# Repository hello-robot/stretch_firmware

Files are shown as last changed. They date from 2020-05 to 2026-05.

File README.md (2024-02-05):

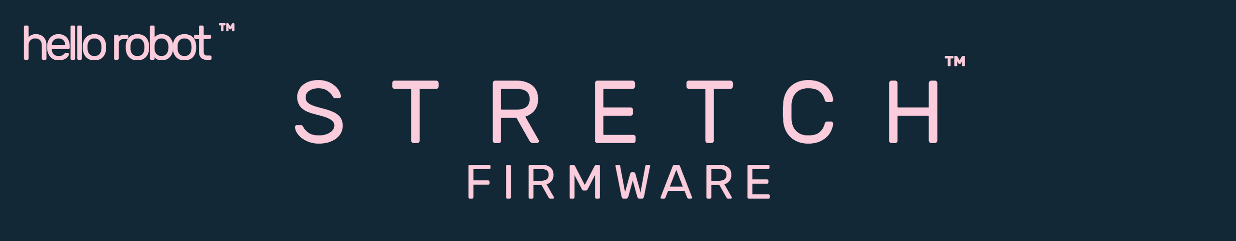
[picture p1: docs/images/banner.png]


# Overview
The [Stretch Firmware](https://github.com/hello-robot/stretch_firmware) repository provides the Arduino based firmware for the Stretch robot. 

Minor version updates to Stretch Body may occasionally require the robot's firmware to also be updated.

The repository includes the firmware for the three Stretch PCBA types: 

* hello_stepper: firmware for stepper motor controller based on the Mechaduino project
* hello_wacc: firmware for wrist accelerometer board (Wacc) in the wrist 
* hello_pimu:  firmware for power and imu board (Pimu) in the base

## License
For details, see the LICENSE.md file in the root directory. All materials within this repository are licensed with the [GNU General Public License v3.0 (GNU GPLv3)](https://www.gnu.org/licenses/gpl-3.0.html) except where other third-party licenses must apply.  

We thank people who have contributed to this work via open-source code and open hardware. We especially thank the [Mechaduino](https://tropical-labs.com/mechaduino/) project and [Tropical Labs](https://tropical-labs.com/). The motor controller firmware and hardware are derived from the excellent [firmware](https://github.com/jcchurch13/Mechaduino-Firmware) and [hardware](https://github.com/jcchurch13/Mechaduino-Hardware) created for the Mechaduino project by Tropical Labs.

------
<div align="center"> All materials are Copyright 2022-2024 by Hello Robot Inc. Hello Robot and Stretch are registered trademarks. The Stretch robots are covered by U.S. Patent 11,230,000 and other patents pending.</div>

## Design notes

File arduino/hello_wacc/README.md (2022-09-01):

# Stretch RE1/RE2 - Wacc Firmware

The Stretch Wacc Firmware runs on the Wacc PCBA found inside the robot arm. Wacc stands for the 'Wrist + Accelerometer' board. The Wacc firmware provides

* Monitoring of the wrist accelerometer
* Monitoring the Arduino expansion header in the wrist

The Wacc expansion header is electrically routed to potentially provide

* Analog in (x1)
* Digital in (x1)
* Digital out (x2)
* Serial SPI 
* Serial I2C 
* Serial UART

See the [Stretch RE1 Hardware User Guide](https://docs.hello-robot.com) for pin-out, electrical, and connector information.

## Using the Expansion DIO Header

### Factory Interface

By default the Expansion DIO header is configured in firmware to provide two digital inputs, two digital outputs, and an analog input. This can be seen in the [Wacc_status](https://github.com/hello-robot/stretch_firmware/blob/master/arduino/hello_wacc/Common.h) structure.

```c
struct __attribute__ ((packed)) Wacc_Status{
  float ax;	//Accelerometer AX
  float ay;	//Accelerometer AY
  float az;	//Accelerometer AZ
  int16_t a0; //expansion header analog in
  uint8_t d0; //expansion header digital in
  uint8_t d1; //expansion header digital in
  uint8_t d2; //expansion header digital out
  uint8_t d3; //expansion header digital out
  uint32_t single_tap_count; //Accelerometer tap count
  uint32_t state;
  uint32_t timestamp; //ms, overflows every 50 days
  uint32_t debug;
};
```

The user can interact with these pins through the [Stretch Body python interface](https://hello-robot.github.io/stretch_body_guide/). 

### Custom Interface

Advanced users may want to create a custom interface to the Expansion DIO header that utilizes SPI, I2C, or UART. For this, see the provided Stretch Firmware tutorials.

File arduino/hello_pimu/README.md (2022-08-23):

# Stretch RE1/RE2 - Pimu Firmware

The Stretch Pimu Firmware runs on the Pimu PCBA. Pimu stands for Power+IMU. The firmware is responsible for 

* Monitoring / filtering / calibration of 9DOF IMU 

* Battery voltage and current monitoring

* Buzzer

* Base case fan control

* Runstop monitoring

* Monitoring cliff sensors

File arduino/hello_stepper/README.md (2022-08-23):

# Stretch RE1/RE2 - Stepper Firmware

The Stretch Stepper Firmware runs on the Stepper PCBA found on the back of the Stretch stepper motors. It is a modified version of the open source [Mechaduino project](https://github.com/jcchurch13/Mechaduino-Firmware), which provides closed loop current control of a stepper motor.

The firmware is organized so as to allow switching, via serial command, between 'stock Mechaduino mode' with its menu interface and the Hello Robot firmware with its RPC interface.

The primary hardware modifications are:

* Higher current capacity by use of parallel motor drivers
* Locking JST connectors
* Addition of a 'sync' line for multi-dof synchronization

The primary software modifications are:

* RPC and serialization layer to manage controller parameters, controller commands, etc

* Trapezoidal trajectory generators based on the library [MotionGenerator](https://github.com/EmanuelFeru/MotionGenerator) 

* Handling of runstop and motor synchronization

* Implementation of a guarded move behavior

* Various controller variants, controller and parameter management functions

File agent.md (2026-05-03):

# Stretch Body AI Directives

You are currently operating inside the `stretch_firmware` repository (Core firmware for the Stretch RE1, Stretch 2, and Stretch 3 robot).

## Ecosystem Navigation
Do not guess hardware specifications or firmware behavior. If a user asks a question that requires knowledge outside of this  codebase, use your file system tools to navigate to the sibling repositories:
* **Master Knowledge Base (Datasheets/Tutorials):** `../stretch_knowledge_base`
* **Firmware Source Code:** `../stretch_body`

If these directories do not exist, politely inform the user that they can clone them from the Hello Robot GitHub into their `~/repos` folder for better assistance.

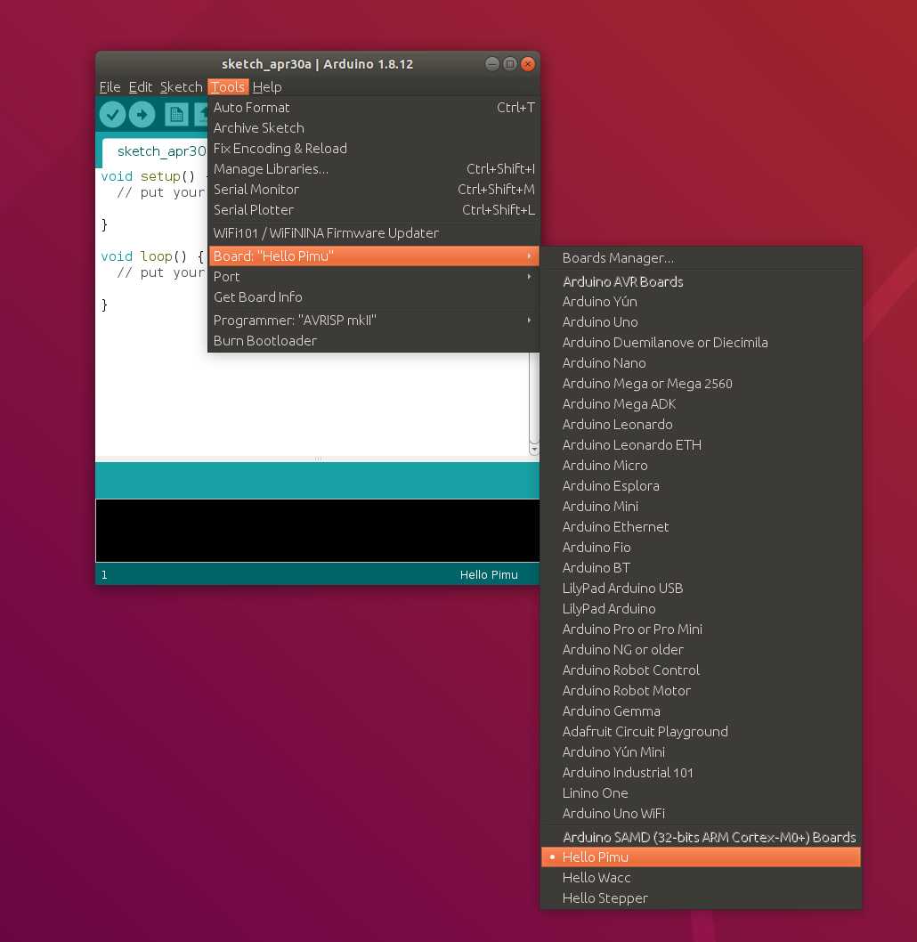
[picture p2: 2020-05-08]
docs/images/arduino-2.png

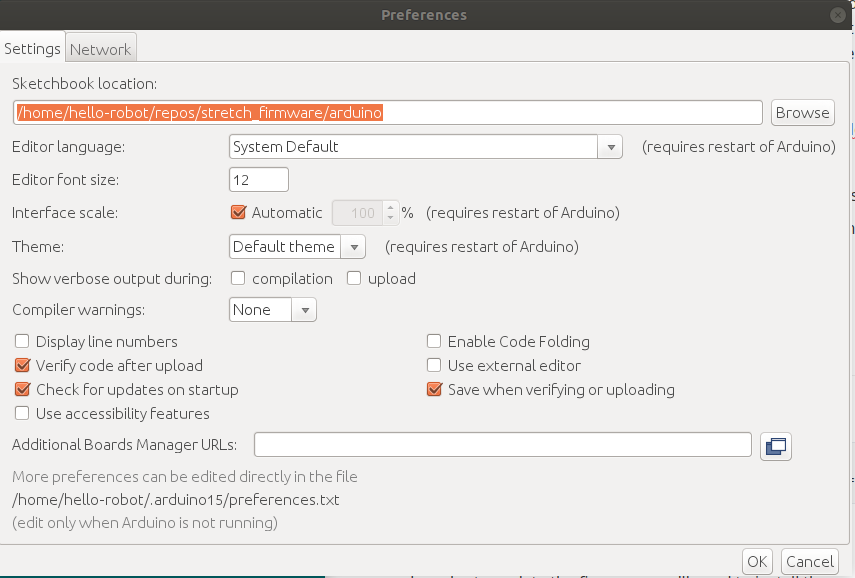
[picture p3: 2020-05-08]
docs/images/arduino-1.png

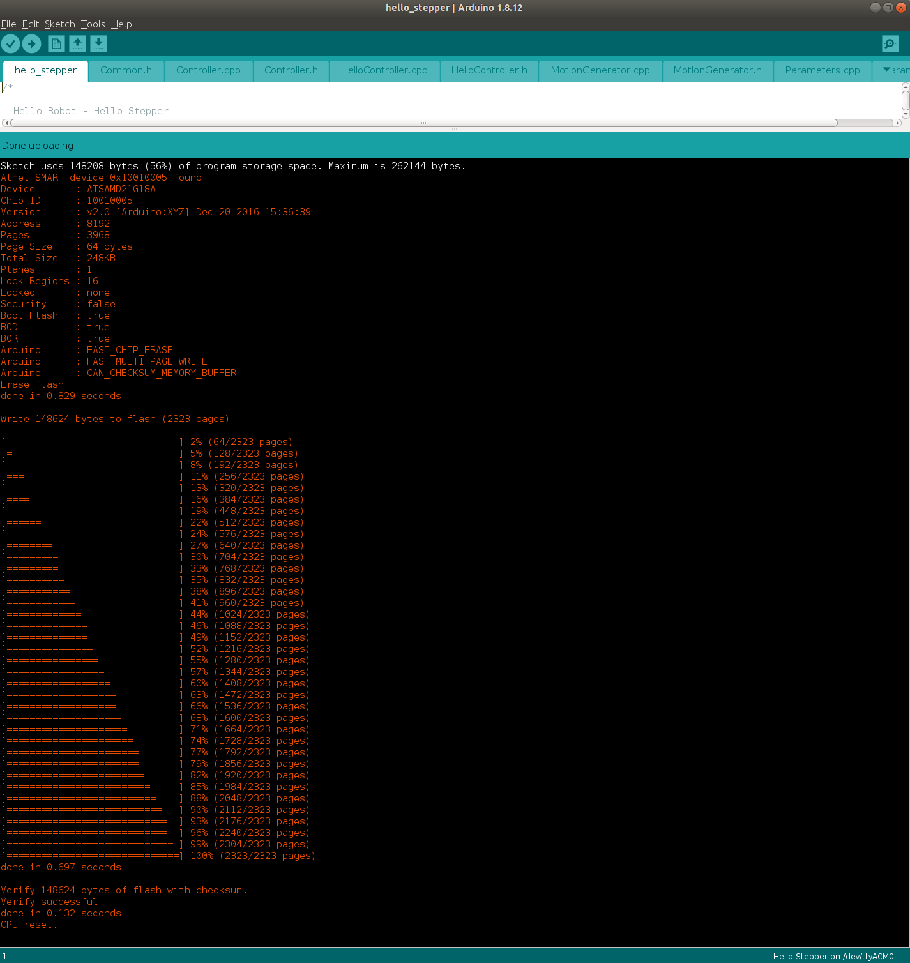
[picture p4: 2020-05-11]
docs/images/arduino-4.png

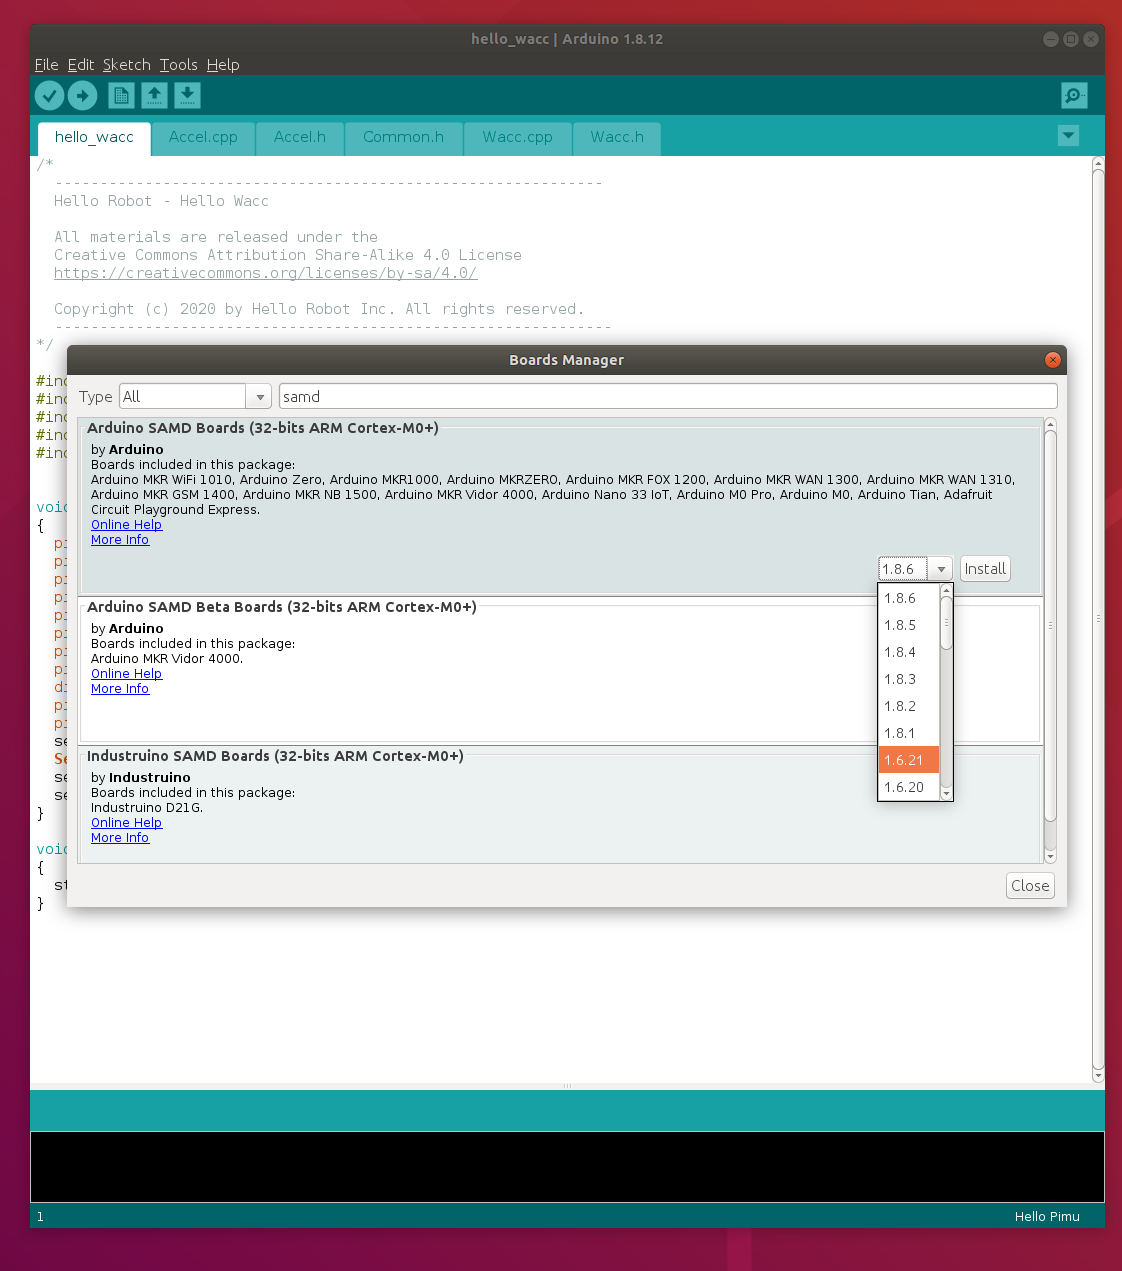
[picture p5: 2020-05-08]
docs/images/arduino-3.png

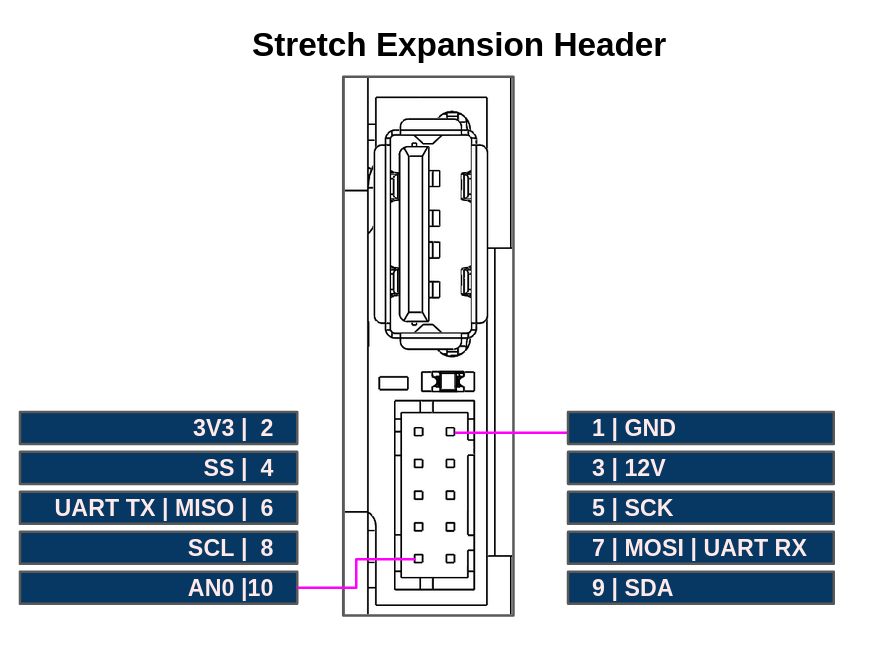
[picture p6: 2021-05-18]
docs/images/wrist_expansion_header.png

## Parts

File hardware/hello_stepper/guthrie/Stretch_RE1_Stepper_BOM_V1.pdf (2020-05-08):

Comment | Description | Designator
Hello_Robot_Logo
S2B-PH-SM4-TB(LF)(SN) | CONN HEADER SMD R/A 2POS 2MM | BRAKE
0.1UF 25V | CAP CER 0.1UF 25V Y5V 0603 | C1, C2, C3, C5, C10, C13, C18, C19
12PF 50V | CAP CER 12PF 50V C0G/NP0 0603 | C7, C8
1UF 25V | CAP CER 1UF 25V X5R 0603 | C9, C11, C12
0.22uF 50V | CAP CER 0.22UF 50V X5R 0603 | C16, C20
100uF 50V | CAP ALUM 100UF 20% 50V SMD | C17
Yellow | LED Yellow CLEAR SMD R/A | DBG
250mA | PTC RESET FUSE 16V 250MA 1206 | F1
0Ohm | JUMPER TIN SMD | GND
| M3 through hole | H1, H2, H3, H4
220 Ohm | FERRITE BEAD 220 OHM 0805 1LN | L1
470 OHM | FERRITE BEAD 470 OHM 0603 1LN | L2
S4B-XH-A(LF)(SN) | CONN HEADER R/A 4POS 2.5MM | MOTOR
HEADER-Shrouded-2X5-P127 | CONN HEADER SMD 10POS 1.27MM | PGM
S3B-XH-A(LF)(SN) | CONN HEADER R/A 3POS 2.5MM | POWER
BSS138 | MOSFET N-CH 60 V 320 mA | Q1
330 | RES SMD 330 OHM 5% 1/4W 0603 | R3
0.1Ohm | RES 0.1 OHM 1% 1/3W 1206 | R5, R6
1K | RES SMD 1K OHM 1% 1/10W 0603 | R7, R8
1MOhm | RES 1M OHM 1% 1/8W 0805 | R10
200K | RES 200K OHM 1% 1/8W 0805 | R11
TACT_Switch_4.2MM | SWITCH TACTILE SPST-NO 0.05A 16V | RESET
RCU-0C | PC TEST POINT NATURAL | T3V3, TGND
AS5047D | ROTARY ENCODER MAGNETIC PROG | U1
AP2112K-3.3TRG1 | IC REG LINEAR 3.3V 600MA SOT25 | U2
SAMD21G18A-AUT | Atmel D21 32bit ARM Cortex-M0 microcontroller - 48 PIN TQFP 256KB flash memory + 32KB SRAM U3
A4950ELJTR-T | IC MOTOR DRIVER 8V-40V 8SOIC | U4, U5
| CONN USB MICRO B RECPT SMT R/A | USB
5V | Varistor 1 Circuit Surface Mount, MLCV 0603 | V1, V2
32.768KHZ | CRYSTAL 32.768KHZ 12.5PF SMD | Y1

Footprint | MF | MPN | Quantity
HELLO_ROBOT_LOGO | | | 1
JST_S2B-PH-SM4-SMT | JST | S2B-PH-SM4-TB(LF)(SN) | 1
0603-CAP | Samsung | CL10F104ZA8NNNC | 8
0603-CAP | Samsung | CL10C120JB8NNNC | 2
0603-CAP | Samsung | CL10A105KA5LNNC | 3
0603-CAP | Murata | GRM188R61H224KAC4D | 2
D8-POL-CAP | Panasonic | EEE-FTH101XAP | 1
CHIPLED_0805_NOOUTLINE - RA | Lite-On | LTST-S220KSKT | 1
1206 | Littelfuse | 1206L025YR | 1
JUMPER_10A_0Ohm | Harwin | S1911-46R | 1
M3_BOLT_HOLE_PAD | | | 4
0805-CAP | MURATA | BLM21PG221SN1D | 1
0603-TDK | MURATA | BLM18PG471SN1D | 1
JST_S4B-XH-A | JST | S4B-XH-A(LF)(SN) | 1
HEADER-2X5-P127 -SMD | Amphenol ICC | 20021521-00010T1LF | 1
JST_S3B-XH-A | JST | S3B-XH-A(LF)(SN) | 1
SOT323 | Nexperia | BSS138PW,115 | 1
0603-RES | Panasonic | ERJ-PA3J331V | 1
1206-RES | Samsung ElectroMechanics | RUT3216FR100CS | 2
0603-RES | Panasonic | ERJ-3EKF1001V | 2
0805-RES | Stackpole | RMCF0805FT1M00 | 1
0805-RES | Stackpole | RMCF0805FT200K | 1
TACT4.2MM | C&K | PTS810 SJM 250 SMTR LFS | 1
PC_TESTPOINT | TE Connectivity | RCU-0C | 2
TSSOP14 | AMS | AS5047D | 1
SOT25 | Diodes Inc | AP2112K-3.3TRG1 | 1
TQFP48-7X7 | Microchip | SAMD21G18A-AUT | 1
SO8_PAD | Allegro | A4950ELJTR-T | 2
MICRO_USB_B_RA_SMT | Amphenol | 10118193-0001LF | 1
0603-RES | Bournes | CG0603MLC-05E | 2
CRYSTAL-2SMD | Diodes Inc | G83270022 | 1

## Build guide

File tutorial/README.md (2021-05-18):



# Overview

These tutorials demonstrate how to use the Stretch wrist expansion header to integrate custom hardware into [Stretch Body](https://docs.hello-robot.com/stretch_body_guide/).

**NOTE** It is possible to brick the Wacc board by incorrectly configuring the hardware peripherals of the SAMD uC. Therefore, when integrating your custom hardware into the Wacc we strongly recommend emulating the Wacc board until the functionality is complete. The tutorial [Wacc Emulation](./wacc_emulation.md) describes how to configure an Adafruit Metro M0 Express to behave as a stand-in for a Wacc board.

| Tutorial | Description |
| --- | --- |
| [Data Transfer](./docs/data_transfer.md) | How to plumb your custom data from the wrist Arduino through Stretch Body |
| [Wrist Board Emulation](./docs/wacc_emulation.md) | How to emulate the Stretch wrist board using an off the shelf Arduino |
| [SPI Sensor](./docs/spi_sensor.md) | How to integrate an SPI sensor |
| [I2C Sensor](./docs/i2c_sensor.md) | How to integrate an I2C sensor |
| [Serial Sensor](./docs/serial_sensor.md) | How to integrate a Serial UART sensor |

**Note: These tutorials require version 0.0.10 or later of Stretch Body. If necessary, please update your install:**

```bash
>>$ pip2 install hello-robot-stretch-body
```

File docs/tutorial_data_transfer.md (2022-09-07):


**NOTE** It is possible to brick the Wacc board by incorrectly configuring the hardware peripherals of the SAMD uC. Therefore, when integrating your custom hardware into the Wacc we strongly recommend emulating the Wacc board until the functionality is complete. The tutorial [Wacc Emulation](./tutorial_wacc_emulation.md) describes how to configure an Adafruit Metro M0 Express to behave as a stand-in for a Wacc board.

**NOTE**: These tutorials may require the latest version of Stretch Body. If necessary, please update your install.

# Integrating Custom Data

In this tutorial we explore how to plumb custom data to and from the Arduino based Stretch Wacc (Wrist + Accelerometer) board. This enables users to integrate custom sensors and actuators on to the [Wrist Expansion header](https://docs.hello-robot.com/0.2/stretch-hardware-guides/docs/hardware_guide_re2/#wrist-expansion-header). 

## How Data Transfer Happens in Stretch Body

Data is transferred between Stretch Body Python and the Arduino based firmware using USB based serial. 

As an example, consider the transfer of a `Status` data message from the Wacc to Stretch Body. This involves:

* Stretch Body requests new Status data via `wacc.pull_status()`
* This generates an RPC call to the Wacc board
* The `status` data on the Wacc board gets 'packed' and transmitted back to Stretch Body
* Stretch Body unpacks the data into the `status` dictionary of the [Wacc Python class](https://github.com/hello-robot/stretch_body/blob/master/body/stretch_body/wacc.py).

Similarly, data can go the other direction (e.g., `Command` messages ).

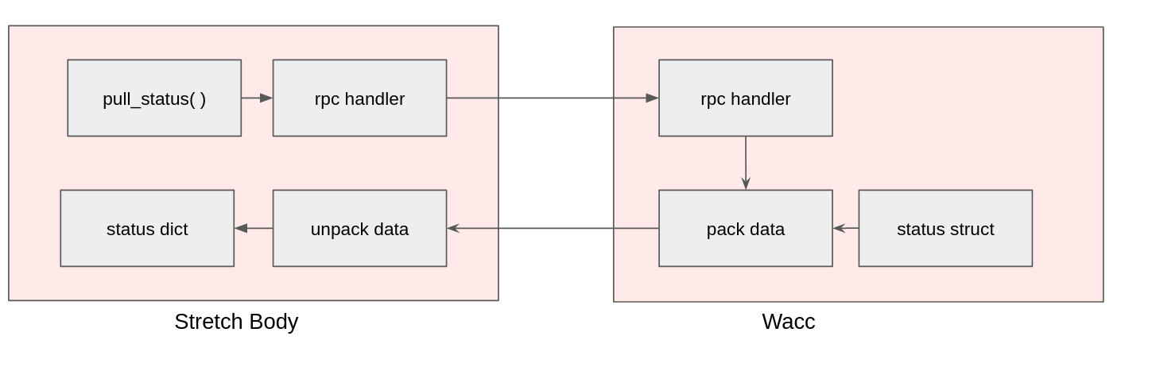
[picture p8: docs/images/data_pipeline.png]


Fortunately, the data transfer is managed automatically for the developer. In order to integrate your custom data you will:

* Extend the firmware  `Status` and `Command` structs to include your data
* Derive your own class from the Stretch Body `Wacc` class that packs and unpacks your custom data

## Calculator Example

As a simple example we will extend the Wacc to be an embedded calculator. The implementation is found in the [Wacc_Calc Arduino sketch](https://github.com/hello-robot/stretch_firmware/tree/master/tutorials/arduino/hello_wacc_calc) and the corresponding [WaccCalc Python class](https://github.com/hello-robot/stretch_firmware/tree/master/tutorials/python/wacc_calc.py).

### Arduino

#### Define data structures
First, we define the data to be sent back and forth in [Common.h](https://stretch_firmware/tree/master/hello-robot/stretch_firmware/tree/master/tutorials/arduino/hello_wacc_calc/Common.h) of the firmware.

```c
struct __attribute__ ((packed)) Calc_Command{
  float var1;
  float var2;
  uint8_t op;
};
struct __attribute__ ((packed)) Calc_Status{
  float result;
};
```

Our calculator will perform the computation: `result=op(var1,var2)`.

Now add these structs to the  `Status` and  `Command` structs in  [Common.h](https://github.com/hello-robot/stretch_firmware/tree/master/tutorials/arduino/hello_wacc_calc/Common.h):

```c
struct __attribute__ ((packed)) Wacc_Command{
  Calc_Command calc;
  ...
};

struct __attribute__ ((packed)) Wacc_Status{
  Calc_Status calc;
  ...
};
```

The ordering of the data is important.  Your custom data should be at the start of the struct as the Python class will unpack this data first.

#### Define calculator function
Next we add the calculator function to  [Wacc.cpp](https://github.com/hello-robot/stretch_firmware/tree/master/tutorials/arduino/hello_wacc_calc/Wacc.cpp):

```c
float my_calc(uint8_t op, float var1, float var2)
{
  if (op==0)
    return var1+var2;
  if (op==1)
    return var1*var2;
  if (op==2)
    return var1/var2;
  return 0;
}
```
#### Integrate calculator into the control loop
Finally, we integrate our calculator into the embedded control loop in [Wacc.cpp](https://github.com/hello-robot/stretch_firmware/tree/master/tutorials/arduino/hello_wacc_calc/Wacc.cpp). 

The function `stepWaccController()` in  [Wacc.cpp](https://github.com/hello-robot/stretch_firmware/tree/master/tutorials/hello_wacc_calc/Wacc.cpp) is called by Timer5 at 700Hz. The calculator is fairly lightweight so its computation time should not interfere with the existing Wacc timing. Heavier computation would require careful integration with an eye to loop timing.

Add the call to `stepWaccController()`  -- just prior to the `Status` data being copied out for transmittal back. 

```c
void stepWaccController()
{
...
stat.calc.result=my_calc(cmd.calc.op,cmd.calc.var1, cmd.calc.var2);
memcpy((uint8_t *) (&stat_out),(uint8_t *) (&stat),sizeof(Wacc_Status));
}
```

The variable `cmd`, which contains the command to the calculator, is automatically updated with fresh data via the RPC mechanism.

#### Bump protocol versions
The packet definition of data exchanged between Python and the Arduino is tagged with a protocol version. This allows the Python Device to ensure it is exchanging compatible data. 

The mainline release of Stretch Firmware starts with protocol version `0` and increments with each new protocol release. To avoid conflicts, for this tutorial we pick an arbitrary large number (99). 

In [Common.h](https://github.com/hello-robot/stretch_firmware/tree/master/tutorials/arduino/hello_wacc_calc/Common.h) , we bump from Protocol '0' 

```c
#define FIRMWARE_VERSION "Wacc.v0.0.1p0"
```

 to Protocol '99'

```c
#define FIRMWARE_VERSION "Wacc.v0.0.1p99"
```

### Python

Now we will implement [WaccCalc](https://github.com/hello-robot/stretch_firmware/tree/master/python/wacc_calc.py) which  derives from the [Wacc Python class](https://github.com/hello-robot/stretch_body/blob/master/body/stretch_body/wacc.py).

```python
from stretch_body.wacc import *
from stretch_body.transport import *

class WaccCalc(Wacc):
    """
    This class demonstrates how to extend the Wacc class with custom data
    See the corresponding tutorial for more information.
    """
    def __init__(self,verbose=False):
        Wacc.__init__(self,verbose=verbose,
                      ext_status_cb=self.ext_unpack_status, #Set callback to unpack status
                      ext_command_cb=self.ext_pack_command) #Set callback to pack command

        self._command['calc']={'op':0,'var1':0,'var2':0} #Extend command dictionary with custom fields
        self.status['calc'] =0.0                         #Extend status dictionary with custom fields
        self.valid_firmware_protocol = 'pMyCalc'

    def calculate(self,op,var1,var2):
        """
        0: addition
        1: multiplication
        2: division
        """
        self._command['calc']['op'] =int(op)
        self._command['calc']['var1']=float(var1)
        self._command['calc']['var2']=float(var2)
        self._dirty_command=True

    def pretty_print(self):
        Wacc.pretty_print(self)
        print 'Calc:',self.status['calc']

    def ext_unpack_status(self,s):
        """
        s: byte array to unpack
        return: number of bytes unpacked
        """
        sidx=0
        self.status['calc'] = unpack_float_t(s[sidx:])
        return 4

    def ext_pack_command(self,s,sidx):
        """
        s: byte array to pack in to
        sidx: index to start packing at
        return: new sidx
        """
        pack_float_t(s, sidx, self._command['calc']['var1'])
        sidx += 4
        pack_float_t(s, sidx, self._command['calc']['var2'])
        sidx += 4
        pack_uint8_t(s, sidx, self._command['calc']['op'])
        sidx += 1
        return sidx

```

The class registers two callbacks for packing `Command` data and unpacking `Status` data.  They are fairly self-explanatory and can be easily extended to match your custom data.  Looking at the unpacking code:
```python
  def ext_unpack_status(self,s):
        """
        s: byte array to unpack
        return: number of bytes unpacked
        """
        sidx=0
        self.status['calc'] = unpack_float_t(s[sidx:])
        return 4
```

, we see the use of `unpack_float_t`. This, and other functions to unpack data, are found in `stretch_body.transport`. 

It is important that the data types and order match exactly those declared in the firmware. For example in  [Common.h](https://github.com/hello-robot/stretch_firmware/tree/master/tutorials/arduino/hello_wacc_calc/Common.h) we have:

```c
struct __attribute__ ((packed)) Calc_Command{
  float var1;
  float var2;
  uint8_t op;
};
```

, and on the Python side we have

```python
pack_float_t(s, sidx, self._command['calc']['var1'])
sidx += 4
pack_float_t(s, sidx, self._command['calc']['var2'])
sidx += 4
pack_uint8_t(s, sidx, self._command['calc']['op'])
sidx += 1
```

## Test the Calculator - iPython

We're ready to try out our calculator. First,

* Install and setup the Arduino IDE if it isn't already as described in the [Updating Firmware tutorial](./tutorial_updating_firmware.md).
* Open the [Wacc_Calc Arduino sketch](https://github.com/hello-robot/stretch_firmware/tree/master/tutorials/arduino/hello_wacc_calc) in the Arduino IDE.  
* Select the `hello_wacc` board, the  `ttyACMx` port that maps to the Wacc board. Then burn the firmware as described in the the [Updating Firmware tutorial](./tutorial_updating_firmware.md).

Now, lets try it out:

```bash
>>$ cd ~/repos/stretch_firmware/tutorial/python/
>>$ ipython
```

And from iPython

```python
In [1]: import wacc_calc
In [2]: w=wacc_calc.WaccCalc()
In [3]: w.startup()
In [4]: w.calculate(op=0,var1=100.0,var2=200.0)
In [5]: w.push_command()
In [6]: w.pull_status()
In [7]: print 'Result is',w.status['calc']
Result is 300.0

In [8]: w.calculate(op=1,var1=100.0,var2=200.0)
In [9]: w.push_command()
In [10]: w.pull_status()
In [11]: print 'Result is',w.status['calc']
Result is 20000.0

In [12]: w.calculate(op=2,var1=100.0,var2=200.0)
In [13]: w.push_command()
In [14]: w.pull_status()
In [15]: print 'Result is',w.status['calc']
Result is 0.5

```

## Test the Calculator - Script

Alternatively you can use the provided tool, [stretch_wacc_calc_jog.py](https://github.com/hello-robot/stretch_firmware/tree/master/tutorials/python/stretch_wacc_calc_jog.py). Here you can use the calculator through the menu.

```bash
hello-robot@stretch-re1-100x:~$ cd repos/stretch_firmware/tutorial/python/
hello-robot@stretch-re1-100x:~/repos/stretch_firmware/tutorial/python$ ./stretch_wacc_calc_jog.py 
------ MENU -------
m: menu
r: reset board
a: set D2 on
b: set D2 off
c: set D3 on
d: set D3 off
X: do calculation
-------------------
X
---Calculate Op(Var1,Var2) ---
Op=0: Add
Op=1: Mult
Op=2: Div
Enter Op
1
Enter Var1
12
Enter Var2
13
```
## 

## Adding YAML Parameters

The `WaccCalc` class can use the Stretch Body YAML files as well. For example, add to your `stretch_re1_user_params.yaml`:

```yaml
wacc:
  calc_scalar: 2.0
```

Now let's scale the commands to the Arduino according to this YAML parameter. In `WaccCalc`:

```python
    def calculate(self,op,var1,var2):
        """
        0: addition
        1: multiplication
        2: division
        """
        self._command['calc']['op'] =int(op)
        self._command['calc']['var1']=self.params['calc_scalar']*float(var1)
        self._command['calc']['var2']=self.params['calc_scalar']*float(var2)
        self._dirty_command=True
```

Run the iPython as above and you'll see the values multiplied by the YAML scalar.

## Final Steps

We want the Stretch Body Robot to use `WaccCalc` and not `Wacc`. To do this, add the following to your `stretch_re1_user_params.yaml`:

```
robot:
  custom_wacc:
    py_class_name: WaccCalc
    py_module_name: wacc_calc
```

This tells Robot which module and class to create its `Wacc` instance from. 

Now, test that it works from iPython

```python
In [1]: import stretch_body.robot

In [2]: robot=stretch_body.robot.Robot()
Starting TransportConnection on: /dev/hello-wacc
In [3]: robot.startup()

In [4]: robot.wacc.calculate(op=0,var1=100.0,var2=200.0)
In [5]: robot.push_command()
In [6]: print 'Result',robot.wacc.status['calc']
Result 300.0

In [7]: robot.stop()

```

------
<div align="center"> All materials are Copyright 2022 by Hello Robot Inc. Hello Robot and Stretch are registered trademarks. The Stretch RE1 and RE2 robots are covered by U.S. Patent 11,230,000 and other patents pending.</div>

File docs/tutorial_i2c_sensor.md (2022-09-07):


**NOTE** It is possible to brick the Wacc board by incorrectly configuring the hardware peripherals of the SAMD uC. Therefore, when integrating your custom hardware into the Wacc we strongly recommend emulating the Wacc board until the functionality is complete. The tutorial [Wacc Emulation](./tutorial_wacc_emulation.md) describes how to configure an Adafruit Metro M0 Express to behave as a stand-in for a Wacc board.

**NOTE**: These tutorials may require the latest version of Stretch Body. If necessary, please update your install.

# Integrating an I2C Device

This tutorial illustrates the integration of a I2C device on to the [Wrist Expansion header](https://docs.hello-robot.com/0.2/stretch-hardware-guides/docs/hardware_guide_re2/#wrist-expansion-header). It extends t. We recommend doing the [Data Transfer](./tutorial_data_transfer.md) tutorial first. 

# Calculator via I2C

In this tutorial we will run the calculator from the [Data Transfer](./tutorial_data_transfer.md) tutorial on an Adafruit Metro M0 Express (Arduino Zero) that is running as an I2C slave. It will take a calculator `Command` from the Wacc and return the result in `Status` message. 

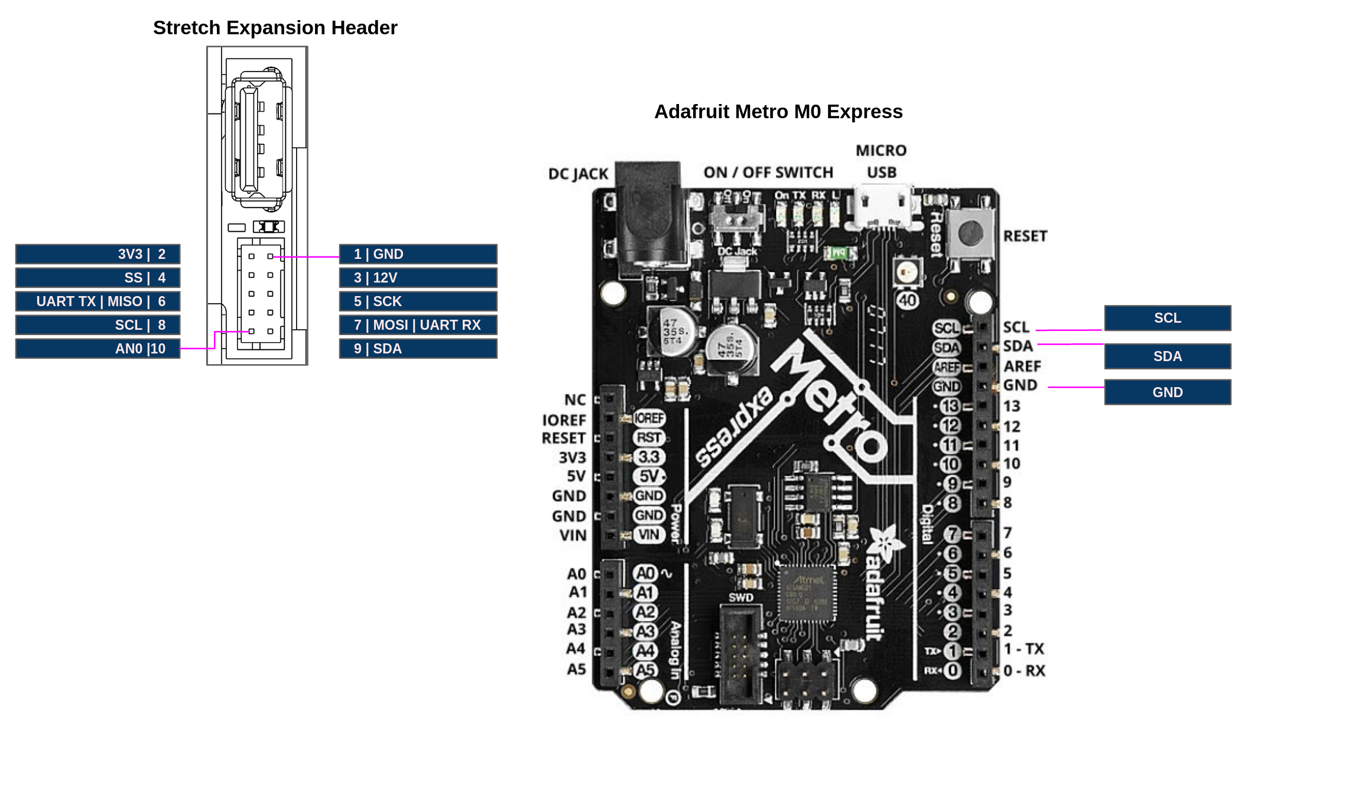
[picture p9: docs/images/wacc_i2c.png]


### Flash Firmware

First, program the Metro with the provided sketch, [zero_wacc_i2c](https://github.com/hello-robot/stretch_firmware/tree/master/tutorials/arduino/zero_wacc_i2c). Be sure to:

* Select the board's port from the IDE under Tools/Port
* Select the board 'Arduino UNO' from the IDE under Tools/Board

Next, program the Wacc with the provided sketch, [hello_wacc_i2c](https://github.com/hello-robot/stretch_firmware/tree/master/tutorials/arduino/hello_wacc_i2c). Be sure to:

* Select the board's port from the IDE under Tools/Port
* Select the board 'Adafruit M0 Express' from the IDE under Tools/Board

### Code Walk-through

The code is straightforward and is a natural extension of the code described in the  [Data Transfer](./tutorial_data_transfer.md) tutorial. A few sections to highlight in the  [hello_wacc_i2c](../arduino/hello_wacc_i2c) sketch are:

In`setupWacc()` we add code to configure the I2C. 

```c
Wire.begin(); 
```

In `Wacc.cpp` we add the I2C code:

```c
#include <Wire.h>

uint8_t i2c_out[9];   //I2C data out
uint8_t i2c_in[9];    //I2C data in
uint8_t ds_i2c_cnt=0; //Down sample counter
float FS_I2C = 10;    //Rate to run transactions (Hz)
int buf_idx=0;

void i2cTransaction()
{
  //Send the commmand
  memcpy(i2c_out, (uint8_t *) (&cmd.calc), sizeof(Calc_Command));
  Wire.beginTransmission(4); // transmit to device #4
  for(int i=0;i<sizeof(Calc_Command);i++)
  {
    Wire.write(i2c_out[i]);
  }
  Wire.endTransmission();    

  //Get the result
  Wire.requestFrom(4, sizeof(Calc_Status));
  int buf_idx=0;
  while (Wire.available() && buf_idx<sizeof(Calc_Status)) // loop through all but the last
  {
    uint8_t x = Wire.read();      
    i2c_in[buf_idx++]=x;
  }
  memcpy((uint8_t *) (&stat.calc),i2c_in,  sizeof(Calc_Status));
}
```

Here, the 9 bytes of the `Calc_Command` are transferred out and the 4 bytes of the `Calc_Status` are received. 

**Note: This simple communication protocol is not robust to handshaking errors, etc**

**Note: The Wacc uses I2C to also communicate with its onboard accelerometer** --  the [ADXL343](https://www.analog.com/media/en/technical-documentation/data-sheets/ADXL343.pdf).  In our example we are using I2C address `4` to communicate with our Metro slave. The ADXL343 is configured to use addrex `0xA6` for a write and `0xA7` for a read.

Finally, we call the `i2cTransaction()` function at a rate of `FS_I2C` by adding to `stepWaccController()`:

```c
 if (ds_i2c_cnt++ >= (FS_CTRL / FS_I2C))
  {
    ds_i2c_cnt = 0;
    i2cTransaction();
  }
```

### Wire Up the Boards

Next, wire the Metro to the Expansion Header as:

| Stretch Expansion Header | Uno  |
| --- | ---- |
| SCL | SCL  |
| SDA | SDA  |
| GND | GND  |

### Test the Calculator

Now, test the setup using the provided tool, [stretch_wacc_calc_jog.py](https://github.com/hello-robot/stretch_firmware/tree/master/tutorials/python/stretch_wacc_calc_jog.py). As shown below, The Metro performs the calculation of 12*13 and the result is report back to Stretch Body.

```bash
hello-robot@stretch-re1-100x:~$ cd repos/stretch_firmware/tutorial/python/
hello-robot@stretch-re1-100x:~/repos/stretch_firmware/tutorial/python$ ./stretch_wacc_calc_jog.py 
------ MENU -------
m: menu
r: reset board
a: set D2 on
b: set D2 off
c: set D3 on
d: set D3 off
X: do calculation
-------------------
X
---Calculate Op(Var1,Var2) ---
Op=0: Add
Op=1: Mult
Op=2: Div
Enter Op
1
Enter Var1
12
Enter Var2
13
------ MENU -------
m: menu
r: reset board
a: set D2 on
b: set D2 off
c: set D3 on
d: set D3 off
X: do calculation
-------------------

------------------------------
Ax (m/s^2) 0.0488623343408
Ay (m/s^2) 0.155020624399
Az (m/s^2) -10.0049753189
A0 349
D0 (In) 0
D1 (In) 1
D2 (Out) 70
D3 (Out) 0
Single Tap Count 26
State  0
Debug 0
Timestamp 1591588745.27
Board version: Wacc.Guthrie.V1
Firmware version: Wacc.v0.0.1pMySPI
Calc: 156.0
------ MENU -------
m: menu
r: reset board
a: set D2 on
b: set D2 off
c: set D3 on
d: set D3 off
X: do calculation
-------------------

```
------
<div align="center"> All materials are Copyright 2022 by Hello Robot Inc. Hello Robot and Stretch are registered trademarks. The Stretch RE1 and RE2 robots are covered by U.S. Patent 11,230,000 and other patents pending.</div>

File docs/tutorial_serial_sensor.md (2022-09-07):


**NOTE** It is possible to brick the Wacc board by incorrectly configuring the hardware peripherals of the SAMD uC. Therefore, when integrating your custom hardware into the Wacc we strongly recommend emulating the Wacc board until the functionality is complete. The tutorial [Wacc Emulation](./tutorial_wacc_emulation.md) describes how to configure an Adafruit Metro M0 Express to behave as a stand-in for a Wacc board.

**NOTE**: These tutorials may require the latest version of Stretch Body. If necessary, please update your install.

# Integrating a Serial Device

This tutorial illustrates the integration of a UART device on to the [Wrist Expansion header](https://docs.hello-robot.com/hardware_user_guide/#wrist). We recommend first reading [Data Transfer](./tutorial_data_transfer.md) tutorial to understand how data is transfered back and forth from Stretch Body to the SAMD uC. 

In this tutorial we will extend the [Stretch Body Wacc](https://github.com/hello-robot/stretch_body/blob/master/body/stretch_body/wacc.py) class to send 10 floats down to the custom serial device. The serial device will echo the 10 floats back up to Stretch Body.

For the purposes of the tutorial we will wire the Wacc up in a loopback configuration as a stand-in for an actual physical serial device.

## Loopback Hardware Setup

Connect the UART TX pin to the UART RX pin of the Stretch Expansion Header (or the Metro M0 if emulating the Wacc). Connector information for the Expansion Header is found in the [Hardware Guide](https://docs.hello-robot.com/hardware_user_guide/#wrist-expansion-header).

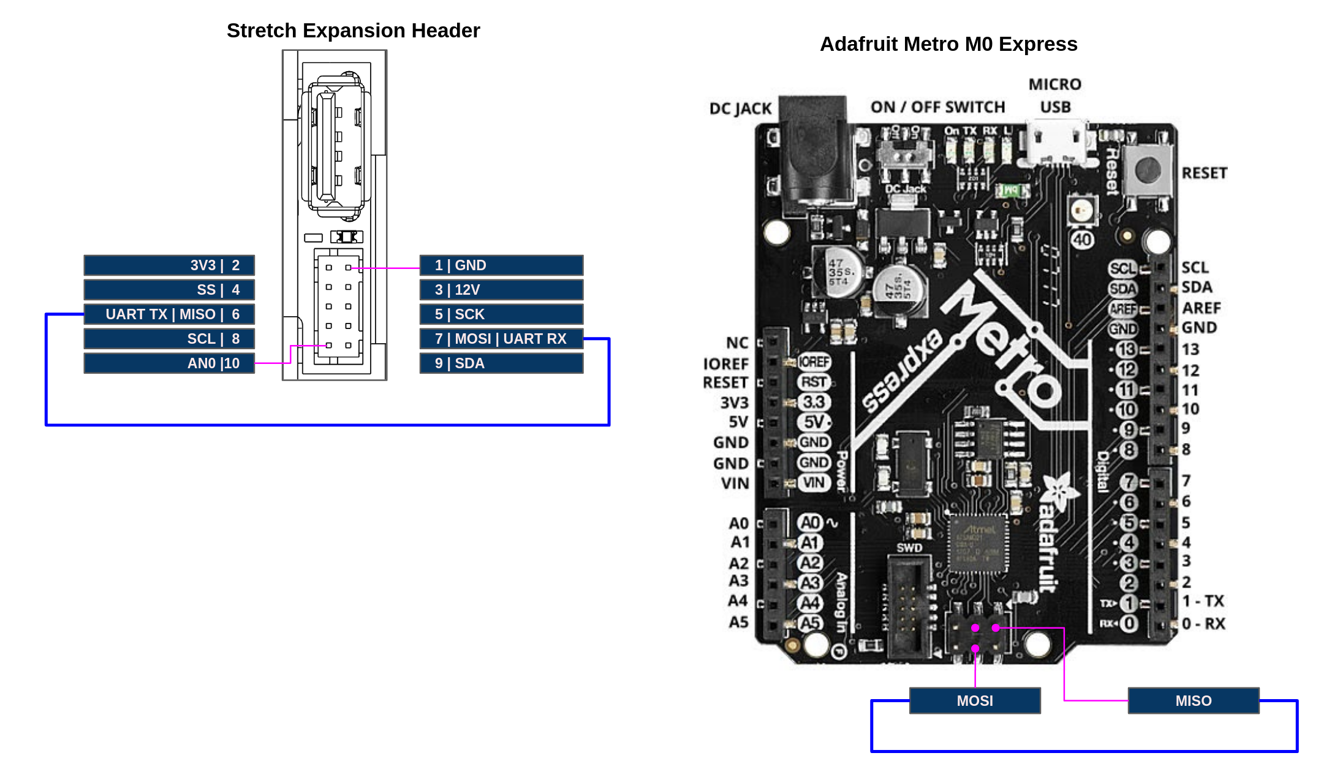
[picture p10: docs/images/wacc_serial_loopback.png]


### Flash Firmware

Pull down the latest version of Stretch Firmware

```bash
>>$ cd ~/repos
>>$ git clone https://github.com/hello-robot/stretch_firmware
```

Next, program the (emulated) Wacc with the provided sketch, [hello_wacc_serial](https://github.com/hello-robot/stretch_firmware/tree/master/tutorials/arduino/hello_wacc_serial). Be sure to:

* Select the board's port from the IDE under Tools/Port
* Select the board 'Hello Wacc' from the IDE under Tools/Board

### Firmware Code Walk-through

First, in the sketch `setup()` we configure enable the SerialExt device

```c
  SerialExt.begin(115200);
```

Next, in [Common.h](https://github.com/hello-robot/stretch_firmware/tree/master/tutorials/arduino/hello_wacc_serial/Common.h) we define Command data to send down from Stretch Body to the serial device. We also define Status data to report back to Stretch Body. For our example we'll send 10 floats down and 10 floats back up.

```c
struct __attribute__ ((packed)) SerialExtCommand{
  float data[10];
};
struct __attribute__ ((packed)) SerialExtStatus{
  float data[10];
};
```

In `Wacc.cpp` we add the code that will communicate with the serial device. Whenever Stretch Body pushes a new command down the Wacc, this function will get called.  Here we are writing the Command data to the SerialExt port. We then send back in the Status message the data we read from SerialExt. As it is a physical loopback connection, the data back in Status will be the same as the Command message.

```c
void serial_comms()
{
  char * data_down=(char*)&(cmd.serial.data[0]);
  char * data_up=(char*)(stat.serial.data);
  for(int i=0;i<40;i++)
  {
    SerialExt.write(data_down+i,1);
  }
  for(int i=0;i<40;i++)
  {
    if (SerialExt.available())
    {
      data_up[i]=SerialExt.read();
    }
  }
}
```

## Stretch Body Code Walk-through

We provide an example class [WaccSerialExt](https://github.com/hello-robot/stretch_firmware/tree/master/tutorials/python/wacc_serial_ext.py) that extends the Wacc class of Stretch Body. This class provides two call backs that will get called on `pull_status` and `push_command` respectively. Here we see the packing and unpacking of the 10 floats found in [Common.h](https://github.com/hello-robot/stretch_firmware/tree/master/tutorials/arduino/hello_wacc_serial/Common.h) 

```python
    def ext_unpack_status(self,s):
        """
        s: byte array to unpack
        return: number of bytes unpacked
        """
        sidx=0
        for i in range(self.n_float):
            self.status['serial_ext'][i] = unpack_float_t(s[sidx:])
            sidx+=4
        return sidx
    
    def ext_pack_command(self,s,sidx):
        """
        s: byte array to pack in to
        sidx: index to start packing at
        return: new sidx
        """
        for i in range(self.n_float):
            pack_float_t(s, sidx, self._command['serial_ext'][i])
            sidx += 4
        return sidx
```

We also define a function that generates a new 'command' down to the serial device. In this case it just increments the 10 floats by one:

```python
    def serial_data_increment(self):
        for i in range(self.n_float):
            self._command['serial_ext'][i] =float(self._command['serial_ext'][i]+1)
        self._dirty_command=True
```

Finally, we do a simple test of the class with the tool [stretch_wacc_serial_jog.py](https://github.com/hello-robot/stretch_firmware/tree/master/tutorials/python/stretch_wacc_serial_jog.py)

```python
from wacc_serial_ext import WaccSerialExt
w=WaccSerialExt()
w.startup()
try:
    while True:
        print('Hit enter to do TX/RX cycle')
        raw_input()
        w.serial_data_increment()
        w.push_command()
        print('TX to SerialExt', w._command['serial_ext'])
        w.pull_status()
        print('RX from SerialExt', w.status['serial_ext'])
except (KeyboardInterrupt, SystemExit):
    w.stop()
```

Run it from the command line and verify that the 10 floats are being command down to your serial device, through the loopback connection, and back, up to the WaccSerialExt class:

```bash
>>$ cd ~/repos/stretch_firmware/tutorial/python
>>$ ./stretch_wacc_serial_jog.py 
Hit enter to do TX/RX cycle
..
('TX to SerialExt', [2.0, 3.0, 4.0, 5.0, 6.0, 7.0, 8.0, 9.0, 10.0, 11.0])
('RX from SerialExt', [1.0, 2.0, 3.0, 4.0, 5.0, 6.0, 7.0, 8.0, 9.0, 10.0])
Hit enter to do TX/RX cycle

('TX to SerialExt', [3.0, 4.0, 5.0, 6.0, 7.0, 8.0, 9.0, 10.0, 11.0, 12.0])
('RX from SerialExt', [2.0, 3.0, 4.0, 5.0, 6.0, 7.0, 8.0, 9.0, 10.0, 11.0])
Hit enter to do TX/RX cycle

..
```

NOTE: It takes one control cycle for the command values to be reported back to the status

------
<div align="center"> All materials are Copyright 2022 by Hello Robot Inc. Hello Robot and Stretch are registered trademarks. The Stretch RE1 and RE2 robots are covered by U.S. Patent 11,230,000 and other patents pending.</div>

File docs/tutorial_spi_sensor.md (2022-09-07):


**NOTE** It is possible to brick the Wacc board by incorrectly configuring the hardware peripherals of the SAMD uC. Therefore, when integrating your custom hardware into the Wacc we strongly recommend emulating the Wacc board until the functionality is complete. The tutorial [Wacc Emulation](./tutorial_wacc_emulation.md) describes how to configure an Adafruit Metro M0 Express to behave as a stand-in for a Wacc board.

**NOTE**: These tutorials may require the latest version of Stretch Body. If necessary, please update your install.

# Integrating an SPI Device

This tutorial illustrates the integration of a SPI device on to the [Wrist Expansion header](https://docs.hello-robot.com/0.2/stretch-hardware-guides/docs/hardware_guide_re2/#wrist-expansion-header). It extends the [Data Transfer](./tutorial_data_transfer.md) tutorial. We recommend doing this tutorial prior to doing this one.

# Calculator via SPI

In this tutorial we will run the calculator from the [Data Transfer](./tutorial_data_transfer.md) tutorial on an Adafruit Metro M0 Express (Arduino Zero) that is running as an SPI slave. It will take a calculator `Command` from the Wacc and return the result in `Status` message. 

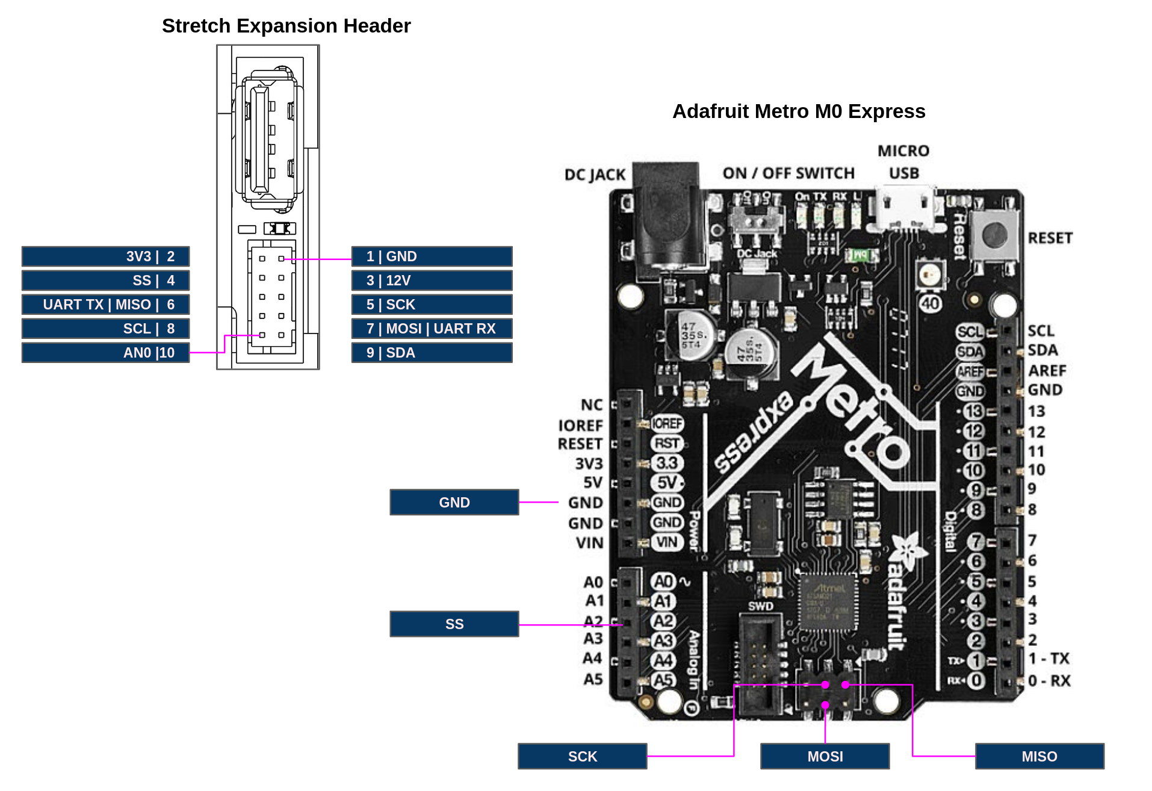
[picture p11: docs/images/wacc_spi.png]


### Flash Firmware

First, program the Metro with the provided sketch, [zero_wacc_spi](https://github.com/hello-robot/stretch_firmware/tree/master/tutorials/arduino/zero_wacc_spi). Be sure to:

* Select the board's port from the IDE under Tools/Port
* Select the board 'Adafruit M0 Express' from the IDE under Tools/Board

Next, program the Wacc with the provided sketch, [hello_wacc_spi](https://github.com/hello-robot/stretch_firmware/tree/master/tutorials/arduino/hello_wacc_spi). Be sure to:

* Select the board's port from the IDE under Tools/Port
* Select the board 'Hello Wacc' from the IDE under Tools/Board

### Code Walk-through

The code is straightforward and is a natural extension of the code described in the  [Data Transfer](./tutorial_data_transfer.md) tutorial. A few sections to highlight in the  [hello_wacc_spi](https://github.com/hello-robot/stretch_firmware/tree/master/tutorials/arduino/hello_wacc_spi) sketch are:

First, in the sketch `setup()` we configure the slave select pin to be an output

```c
pinMode(HEADER_SPI_SS,OUTPUT);
```

Next in `setupWacc()` we add code to configure the SPI

```c
SPISettings settingsA(100000, MSBFIRST, SPI_MODE1);
SPI.begin();
SPI.beginTransaction(settingsA);
```

In `Wacc.cpp` we add the SPI code:

```c
#include <SPI.h>

uint8_t spi_out[9];   //SPI data out
uint8_t spi_in[9];    //SPI data in
uint8_t ds_spi_cnt=0; //Down sample counter
float FS_SPI = 10;    //Rate to run transactions (Hz)

void spiTransaction()
{
  digitalWrite(HEADER_SPI_SS, LOW);
  SPI.transfer('X'); //Mark start of transaction
  memcpy(spi_out, (uint8_t *) (&cmd.calc), sizeof(Calc_Command));
  for (uint8_t idx = 0; idx < 9; idx++)
    spi_in[idx] = SPI.transfer(spi_out[idx]);
  digitalWrite(HEADER_SPI_SS, HIGH);
  memcpy((uint8_t *) (&stat.calc),spi_in+1,  sizeof(Calc_Status));
}
```

Here, the 9 bytes of the `Calc_Command` are transferred out and the 4 bytes of the `Calc_Status` are received. 

**Note: This simple communication protocol is not robust, using an 'X' to demarcate the start of a transaction**

Finally, we call the `spiTransaction()` function at a rate of `FS_SPI` by adding to `stepWaccController()`:

```c
 if (ds_spi_cnt++ >= (FS_CTRL / FS_SPI))
  {
    ds_spi_cnt = 0;
    spiTransaction();
  }
```

### Wire Up the Boards

Next, wire the Metro to the Expansion Header as:

| Stretch Expansion Header | Uno  |
| --- | ---- |
| SS | SS |
| MISO | MISO |
| MOSI | MOSI |
| SCK | SCK  |
| GND | GND  |

**Note: Other Arduino boards can be used. However 5V Arduinos boards will need their SPI lines level shifted to 3V3.**

### Test the Calculator

Now, test the setup using the provided tool, [stretch_wacc_calc_jog.py](https://github.com/hello-robot/stretch_firmware/tree/master/tutorials/python/stretch_wacc_calc_jog.py). As shown below, The Arduino Uno performs the calculation of 12*13 and the result is report back to Stretch Body.

```bash
hello-robot@stretch-re1-100x:~$ cd repos/stretch_firmware/tutorial/python/
hello-robot@stretch-re1-100x:~/repos/stretch_firmware/tutorial/python$ ./stretch_wacc_calc_jog.py 
------ MENU -------
m: menu
r: reset board
a: set D2 on
b: set D2 off
c: set D3 on
d: set D3 off
X: do calculation
-------------------
X
---Calculate Op(Var1,Var2) ---
Op=0: Add
Op=1: Mult
Op=2: Div
Enter Op
1
Enter Var1
12
Enter Var2
13
------ MENU -------
m: menu
r: reset board
a: set D2 on
b: set D2 off
c: set D3 on
d: set D3 off
X: do calculation
-------------------

------------------------------
Ax (m/s^2) 0.0488623343408
Ay (m/s^2) 0.155020624399
Az (m/s^2) -10.0049753189
A0 349
D0 (In) 0
D1 (In) 1
D2 (Out) 70
D3 (Out) 0
Single Tap Count 26
State  0
Debug 0
Timestamp 1591588745.27
Board version: Wacc.Guthrie.V1
Firmware version: Wacc.v0.0.1pMySPI
Calc: 156.0
------ MENU -------
m: menu
r: reset board
a: set D2 on
b: set D2 off
c: set D3 on
d: set D3 off
X: do calculation
-------------------

```

------
<div align="center"> All materials are Copyright 2022 by Hello Robot Inc. Hello Robot and Stretch are registered trademarks. The Stretch RE1 and RE2 robots are covered by U.S. Patent 11,230,000 and other patents pending.</div>

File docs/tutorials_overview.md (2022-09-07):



# Integrating Custom Hardware

These tutorials demonstrate how to use the Stretch wrist expansion header to integrate custom hardware into [Stretch Body](https://github.com/hello-robot/stretch_body).

**NOTE** It is possible to brick the Wacc board by incorrectly configuring the hardware peripherals of the SAMD uC. 
Therefore, when integrating your custom hardware into the Wacc we strongly recommend emulating the Wacc board until the functionality is complete. 
The tutorial [Wacc Emulation](./tutorial_wacc_emulation.md) describes how to configure an Adafruit Metro M0 Express to behave as a stand-in for a Wacc board.

| Tutorial | Description |
|---| --- |
| [Data Transfer](./tutorial_data_transfer.md) | How to plumb your custom data from the wrist Arduino through Stretch Body |
| [Wrist Board Emulation](./tutorial_wacc_emulation.md) | How to emulate the Stretch wrist board using an off the shelf Arduino |
| [SPI Sensor](./tutorial_spi_sensor.md) | How to integrate an SPI sensor |
| [I2C Sensor](./tutorial_i2c_sensor.md) | How to integrate an I2C sensor |
| [Serial Sensor](./tutorial_serial_sensor.md) | How to integrate a Serial UART sensor |

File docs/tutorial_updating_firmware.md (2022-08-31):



# Updating Stretch Firmware

Stretch has 6 Arduino based microcontroller boards that may require a firmware update:

| Board | USB Device | Arduino Sketch |
| --- | --- | --- |
| Left wheel stepper  | /dev/hello-motor-left-wheel  | hello_stepper.ino |
| Right wheel stepper | /dev/hello-motor-right-wheel | hello_stepper.ino |
| Lift stepper | /dev/hello-motor-lift | hello_stepper.ino |
| Arm stepper | /dev/hello-motor-arm | hello_stepper.ino |
| Pimu | /dev/hello-pimu | hello_pimu.ino |
| Wacc | /dev/hello-wacc | hello_wacc.ino |

Firmware updates are managed through the [REx_firmware_updater.py](https://github.com/hello-robot/stretch_factory/blob/master/python/bin/REx_firmware_updater.py) tool, which uses the [Arduino Cli](https://github.com/arduino/arduino-cli) tool to flash the firmware.

Before doing an upgrade first ensure the latest Stretch Body is installed as well as Stretch Factory

```bash
>>$ pip install  hello-robot-stretch-factory --upgrade --no-cache-dir
>>$ pip install  hello-robot-stretch-body --upgrade --no-cache-dir
```
## Firmware Update Tool

The firmware update tool will automatically recommend and install the latest version of firmware found on GitHub. It will only recommend versions that are compatible with the currently installed Stretch Body.

```bash
>>$ REx_firmware_updater.py --help
usage: REx_firmware_updater.py [-h]
                               [--current | --available | --recommended | --install | --install_version | --install_branch | --install_path INSTALL_PATH | --mgmt]
                               [--pimu] [--wacc] [--arm] [--lift]
                               [--left_wheel] [--right_wheel]

Upload Stretch firmware to microcontrollers

optional arguments:
  -h, --help            show this help message and exit
  --current             Display the currently installed firmware versions
  --available           Display the available firmware versions
  --recommended         Display the recommended firmware
  --install             Install the recommended firmware
  --install_version     Install a specific firmware version
  --install_branch      Install the HEAD of a specific branch
  --install_path        INSTALL_PATH Install the firmware on the provided path (eg ./stretch_firmware/arduino)
  --mgmt                Display overview on firmware management
  --pimu                Upload Pimu firmware
  --wacc                Upload Wacc firmware
  --arm                 Upload Arm Stepper firmware
  --lift                Upload Lift Stepper firmware
  --left_wheel          Upload Left Wheel Stepper firmware
  --right_wheel         Upload Right Wheel Stepper firmware
```
## Updating to the Latest Firmware
To update to the latest version of firmware:

```bash
>>$ REx_firmware_updater.py --install
Collecting information...
######################################## Recommended Firmware Updates ########################################

DEVICE                    | INSTALLED                 | RECOMMENDED               | ACTION                    
--------------------------------------------------------------------------------------------------------------
HELLO-WACC                | Wacc.v0.0.2p1             | Wacc.v0.0.1p0             | Downgrade recommended     
HELLO-MOTOR-LIFT          | Stepper.v0.1.0p1          | Stepper.v0.0.4p0          | Downgrade recommended     
HELLO-PIMU                | Pimu.v0.0.2p1             | Pimu.v0.0.1p0             | Downgrade recommended     
HELLO-MOTOR-ARM           | Stepper.v0.1.0p1          | Stepper.v0.0.4p0          | Downgrade recommended     
HELLO-MOTOR-LEFT-WHEEL    | Stepper.v0.1.0p1          | Stepper.v0.0.4p0          | Downgrade recommended     
HELLO-MOTOR-RIGHT-WHEEL   | Stepper.v0.1.0p1          | Stepper.v0.0.4p0          | Downgrade recommended   
######################################### UPDATING FIRMWARE TO... ###########################################
HELLO-WACC                | Downgrading to Wacc.v0.0.1p0             
HELLO-MOTOR-LEFT-WHEEL    | Downgrading to Stepper.v0.0.4p0          
HELLO-MOTOR-RIGHT-WHEEL   | Downgrading to Stepper.v0.0.4p0          
HELLO-MOTOR-LIFT          | Downgrading to Stepper.v0.0.4p0          
HELLO-PIMU                | Downgrading to Pimu.v0.0.1p0             
HELLO-MOTOR-ARM           | Downgrading to Stepper.v0.0.4p0          
------------------------------------------------
WARNING: (1) Updating robot firmware should only be done by experienced users
WARNING: (2) Do not have other robot processes running during update
WARNING: (3) Leave robot powered on during update
WARNING: (4) Ensure Lift has support clamp in place
WARNING: (5) Lift may make a loud noise during programming. This is normal.
Proceed with update?? [y/N]: 
```
Review the recommendations and warnings before proceeding ('y'). If you prefer to only update one or more boards you can specify it on the command line. For example:
```bash
REx_firmware_updater.py --install --arm --wacc
```
## Other Useful Commands

Running  `REx_firmware_updater.py --current` will report the currently install firmware: 
```bash
>>$REx_firmware_updater.py --current
######################################## Currently Installed Firmware ########################################
------------ HELLO-WACC ------------
Installed Firmware: Wacc.v0.0.2p1
Installed Stretch Body supports protocols: p0 , p1
Installed protocol p1 : VALID
------------ HELLO-MOTOR-LIFT ------------
Installed Firmware: Stepper.v0.1.0p1
Installed Stretch Body supports protocols: p0 , p1
Installed protocol p1 : VALID
------------ HELLO-PIMU ------------
Installed Firmware: Pimu.v0.0.2p1
Installed Stretch Body supports protocols: p0 , p1
Installed protocol p1 : VALID
------------ HELLO-MOTOR-ARM ------------
Installed Firmware: Stepper.v0.1.0p1
Installed Stretch Body supports protocols: p0 , p1
Installed protocol p1 : VALID
------------ HELLO-MOTOR-LEFT-WHEEL ------------
Installed Firmware: Stepper.v0.1.0p1
Installed Stretch Body supports protocols: p0 , p1
Installed protocol p1 : VALID
------------ HELLO-MOTOR-RIGHT-WHEEL ------------
Installed Firmware: Stepper.v0.1.0p1
Installed Stretch Body supports protocols: p0 , p1
Installed protocol p1 : VALID

```

Running  `REx_firmware_updater.py --available` will list the available versions on GitHub:

```bash
>>$ REx_firmware_updater.py --available
Collecting information...
####################### Currently Tagged Versions of Stretch Firmware on Master Branch #######################
---- HELLO-WACC ----
Wacc.v0.0.1p0
---- HELLO-MOTOR-LIFT ----
Stepper.v0.0.1p0
Stepper.v0.0.2p0
Stepper.v0.0.3p0
Stepper.v0.0.4p0
---- HELLO-PIMU ----
Pimu.v0.0.1p0
---- HELLO-MOTOR-ARM ----
Stepper.v0.0.1p0
Stepper.v0.0.2p0
Stepper.v0.0.3p0
Stepper.v0.0.4p0
---- HELLO-MOTOR-LEFT-WHEEL ----
Stepper.v0.0.1p0
Stepper.v0.0.2p0
Stepper.v0.0.3p0
Stepper.v0.0.4p0
---- HELLO-MOTOR-RIGHT-WHEEL ----
Stepper.v0.0.1p0
Stepper.v0.0.2p0
Stepper.v0.0.3p0
Stepper.v0.0.4p0
```

------
<div align="center"> All materials are Copyright 2022 by Hello Robot Inc. Hello Robot and Stretch are registered trademarks. The Stretch RE1 and RE2 robots are covered by U.S. Patent 11,230,000 and other patents pending.</div>

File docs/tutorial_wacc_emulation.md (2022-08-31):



# Emulating the Wacc

In this tutorial we describe how to emulate the Arduino based Stretch Wacc (Wrist + Accelerometer) board using an off-the-shelf Arduino. This enables users to develop and test custom code for the Wacc board prior to deploying it to the actual robot hardware.

Emulation involves:

* Installing the Wacc firmware on an Arduino Zero compatible board ( [Adafruit Metro M0 Express](https://www.adafruit.com/product/3505) )
* Mapping the UDEV rules to the Metro

This tutorial assumes the Metro board is plugged into one of Stretch's external USB ports. It is also possible to install Stretch Body on a developer Ubuntu machine if the robot is not available (see below).

# Hardware

We will emulate the Wacc on the Metro board as both boards use the Atmel SAMD21G18A-AUT processor.  

The primary difference between the Wacc and the Metro is that the Wacc integrates an ADXL343 3 axis accelerometer on its I2C bus. As this chip isn't interfaced to our emulation hardware, this data will be missing. The Wacc also lacks the On/Off switch and RGB LED of the Metro.

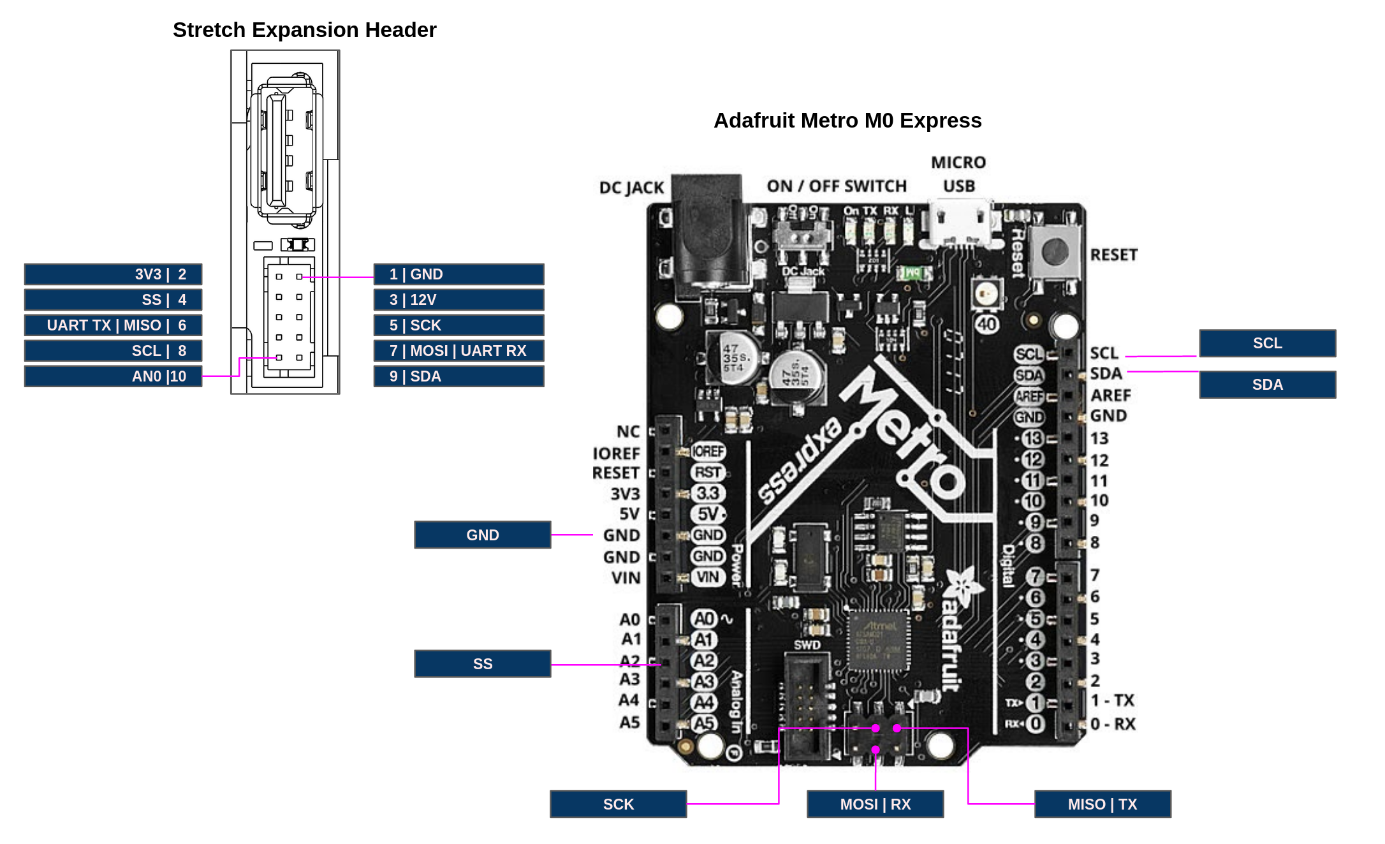
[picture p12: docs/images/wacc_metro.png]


Only a subset of its pins of the Wacc (shown below) are used compared to the Metro. You can attach your custom hardware to the Metro as if it were the Stretch Expansion Header.

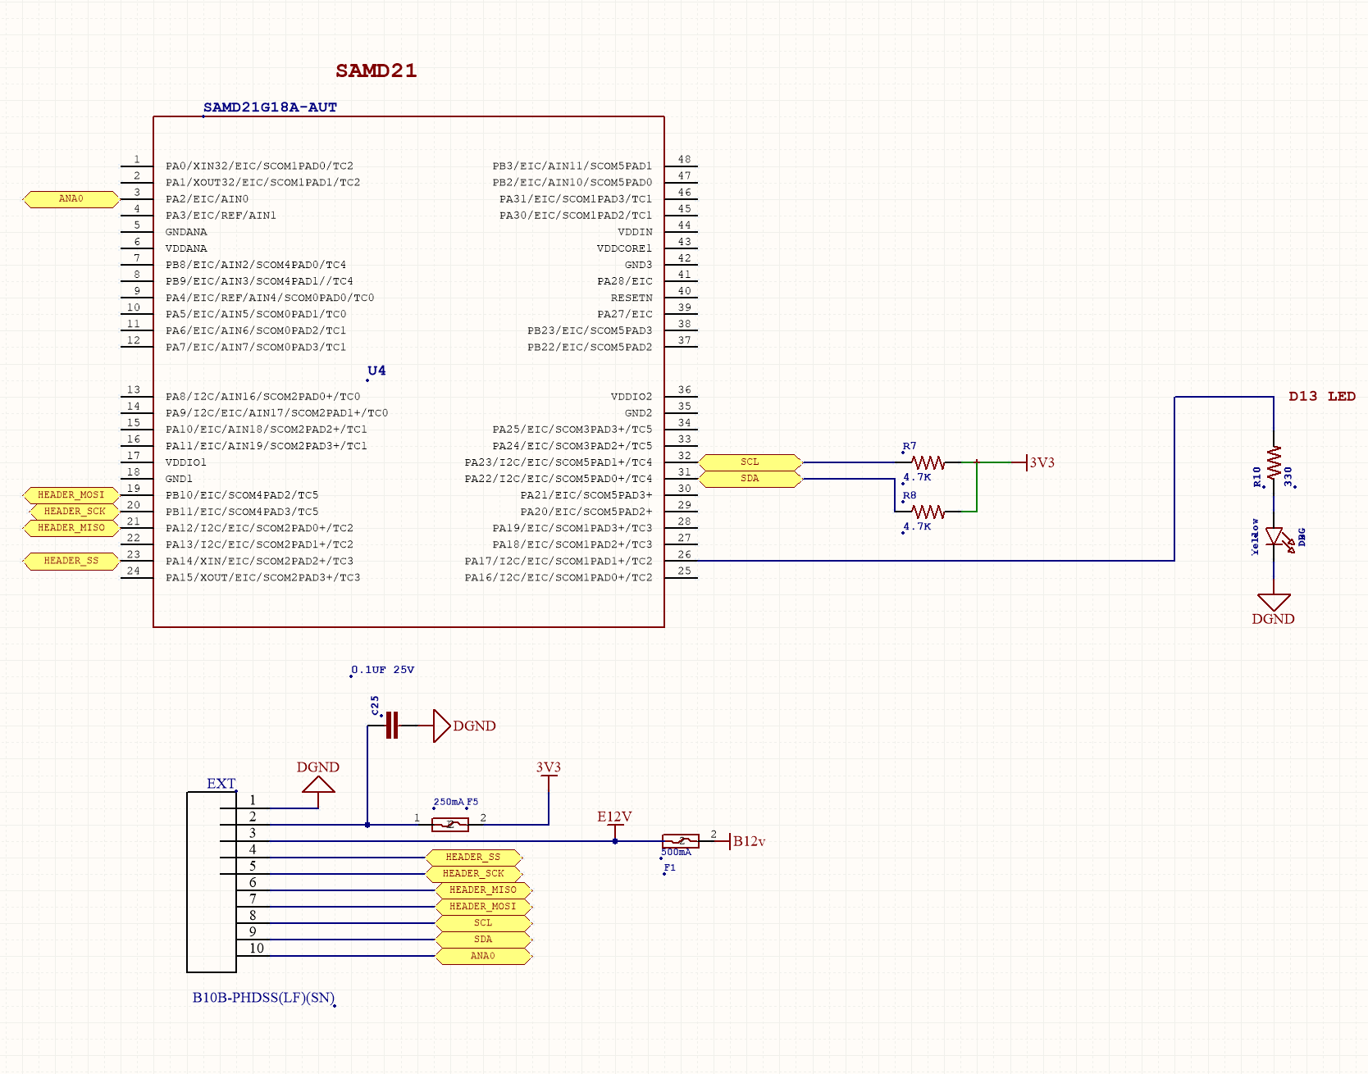
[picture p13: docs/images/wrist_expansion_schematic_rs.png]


# Firmware

First, we'll install the factory Wacc firmware on the Metro. Custom Wacc firmware could be installed using the same process.

First, download the firmware repo onto the development machine if it isn't already there:

```bash
>>$ cd ~/repos
>>$ git clone https://github.com/hello-robot/stretch_firmware
```

Next, install and setup the Arduino IDE has described [here](https://github.com/hello-robot/stretch_install/blob/master/factory/stretch_install_arduino.sh).

Now, with the Metro M0 plugged in to a USB port on Stretch:

* Open the [hello_wacc](https://github.com/hello-robot/stretch_firmware/tree/master/arduino/hello_wacc/hello_wacc.ino) sketch
* Select Tools/Board/Hello Wacc
* Select the Metro board under Tools/Port 
* Upload the firmware. The red LED on the Metro should flash at 1Hz.

Note: Take care to not accidentally burn firmware to the wrong board. You can check the mapping of boards to ports by:

```
>>$ ls -l /dev/hello*
```

# Setup UDEV

Next we need for the Metro to appear as a device named `/dev/hello-wacc`. For this:

* Run 'sudo dmesg -c' to clear the system log
* Hit the reset button on the Metro
* Run 'sudo dmesg | grep Serial

You'll see the Metro serial number:

```bash
>>$ sudo dmesg -c | grep Serial
[810971.303719] usb 1-3: New USB device strings: Mfr=1, Product=2, SerialNumber=3
[810971.303725] usb 1-3: SerialNumber: 9261CC655150484735202020FF0C270C

```

Copy the serial number.  Edit the udev file:

```bash
>>$ sudo nano /etc/udev/rules.d/95-hello-arduino.rules
```

Find the entry for `hello-wacc` and update `ATTRS{serial}` to the new serial number.

```bash
KERNEL=="ttyACM*", ATTRS{idVendor}=="2341", ATTRS{idProduct}=="804d",MODE:="0666", ATTRS{serial}=="SERIAL", SYMLINK+="hello-wacc", ENV{ID_MM_DEVICE_IGNORE}="1"
```

, where SERIAL is the serial number captured from dmesg.

Now reload the udev rule

```bash
>>$ sudo udevadm control --reload
```

Now hit the reset button of the Metro and check that it is mapped:

```bash
>>$ ls -l /dev/hello-wacc 
lrwxrwxrwx 1 root root 7 Jun 10 20:04 /dev/hello-wacc -> ttyACM0
```

**Note: When switching back to Stretch's internal Wacc board you'll need to restore the UDEV file.** This can be done by:

```bash
>>$ sudo cp $HELLO_FLEET_PATH/$HELLO_FLEET_ID/udev/95-hello-arduino.rules /etc/udev/rules.d/
```

# Test the Emulated Wacc

Now, check that your emulated Wacc is working. You should see the Timestamp and A0 values moving when you hit 'Enter'. Now you're ready to integrate your custom hardware.

```bash
>>$ stretch_wacc_jog.py 
------ MENU -------
m: menu
r: reset board
a: set D2 on
b: set D2 off
c: set D3 on
d: set D3 off
-------------------

------------------------------
Ax (m/s^2) 0.0
Ay (m/s^2) 0.0
Az (m/s^2) 0.0
A0 375
D0 (In) 1
D1 (In) 1
D2 (Out) 0
D3 (Out) 0
Single Tap Count 0
State  0
Debug 0
Timestamp 1591846120.85
Board version: Wacc.Guthrie.V1
Firmware version: Wacc.v0.0.1p0

```

------
<div align="center"> All materials are Copyright 2022 by Hello Robot Inc. Hello Robot and Stretch are registered trademarks. The Stretch RE1 and RE2 robots are covered by U.S. Patent 11,230,000 and other patents pending.</div>

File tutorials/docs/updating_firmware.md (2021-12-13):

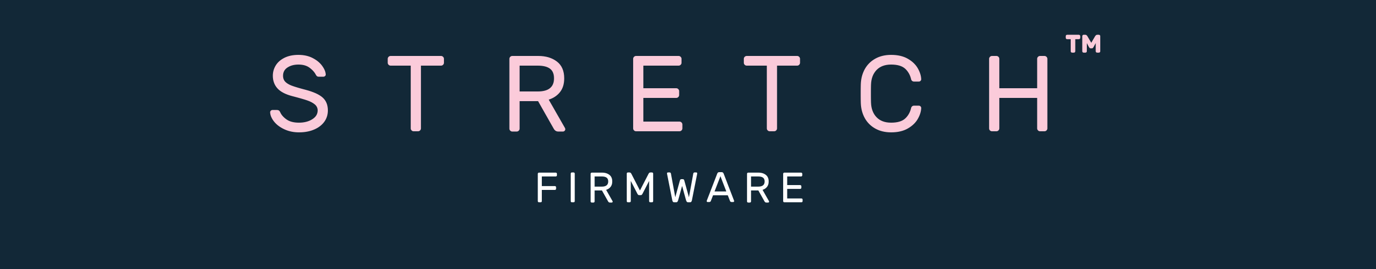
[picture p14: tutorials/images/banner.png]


# Updating Stretch Firmware

Stretch has 6 Arduino based microcontroller boards that may require a firmware update:

| Board | USB Device | Arduino Sketch |
| --- | --- | --- |
| Left wheel stepper  | /dev/hello-motor-left-wheel  | hello_stepper.ino |
| Right wheel stepper | /dev/hello-motor-right-wheel | hello_stepper.ino |
| Lift stepper | /dev/hello-motor-lift | hello_stepper.ino |
| Arm stepper | /dev/hello-motor-arm | hello_stepper.ino |
| Pimu | /dev/hello-pimu | hello_pimu.ino |
| Wacc | /dev/hello-wacc | hello_wacc.ino |

Firmware updates are managed through the [RE1_firmware_updater.py](https://github.com/hello-robot/stretch_factory/blob/master/python/bin/RE1_firmware_updater.py) tool, which uses the [Arduino Cli](https://github.com/arduino/arduino-cli) tool to flash the firmware.

Before doing an upgrade first ensure the latest Stretch Body is installed as well as Stretch Factory

```bash
>>$ pip install  hello-robot-stretch-factory --upgrade --no-cache-dir
>>$ pip install  hello-robot-stretch-body --upgrade --no-cache-dir
```
## Firmware Update Tool

The firmware update tool will automatically recommend and install latest version of firmware found on GitHub. It will only recommend versions that are compatible with the currently installed Stretch Body. **Note: The firmware updater only works on Ubuntu 18.04 currently. Attempting to use the latest version of the firmware updater in Ubuntu 20.04 will error out.**

```bash
>>$ RE1_firmware_updater.py --help
usage: RE1_firmware_updater.py [-h]
                               [--current | --available | --recommended | --install | --install_version | --install_branch | --install_path INSTALL_PATH | --mgmt]
                               [--pimu] [--wacc] [--arm] [--lift]
                               [--left_wheel] [--right_wheel]

Upload Stretch firmware to microcontrollers

optional arguments:
  -h, --help            show this help message and exit
  --current             Display the currently installed firmware versions
  --available           Display the available firmware versions
  --recommended         Display the recommended firmware
  --install             Install the recommended firmware
  --install_version     Install a specific firmware version
  --install_branch      Install the HEAD of a specific branch
  --install_path        INSTALL_PATH Install the firmware on the provided path (eg ./stretch_firmware/arduino)
  --mgmt                Display overview on firmware management
  --pimu                Upload Pimu firmware
  --wacc                Upload Wacc firmware
  --arm                 Upload Arm Stepper firmware
  --lift                Upload Lift Stepper firmware
  --left_wheel          Upload Left Wheel Stepper firmware
  --right_wheel         Upload Right Wheel Stepper firmware
```
## Updating to the Latest Firmware
To update to the latest version of firmware:
 ```bash
>>$ RE1_firmware_updater.py --install
Collecting information...

######################################## Recommended Firmware Updates ########################################

DEVICE                    | INSTALLED                 | RECOMMENDED               | ACTION                    
--------------------------------------------------------------------------------------------------------------
HELLO-WACC                | Wacc.v0.0.2p1             | Wacc.v0.0.1p0             | Downgrade recommended     
HELLO-MOTOR-LIFT          | Stepper.v0.1.0p1          | Stepper.v0.0.4p0          | Downgrade recommended     
HELLO-PIMU                | Pimu.v0.0.2p1             | Pimu.v0.0.1p0             | Downgrade recommended     
HELLO-MOTOR-ARM           | Stepper.v0.1.0p1          | Stepper.v0.0.4p0          | Downgrade recommended     
HELLO-MOTOR-LEFT-WHEEL    | Stepper.v0.1.0p1          | Stepper.v0.0.4p0          | Downgrade recommended     
HELLO-MOTOR-RIGHT-WHEEL   | Stepper.v0.1.0p1          | Stepper.v0.0.4p0          | Downgrade recommended     

########################################## UPDATING FIRMWARE TO... ###########################################
HELLO-WACC                | Downgrading to Wacc.v0.0.1p0             
HELLO-MOTOR-LEFT-WHEEL    | Downgrading to Stepper.v0.0.4p0          
HELLO-MOTOR-RIGHT-WHEEL   | Downgrading to Stepper.v0.0.4p0          
HELLO-MOTOR-LIFT          | Downgrading to Stepper.v0.0.4p0          
HELLO-PIMU                | Downgrading to Pimu.v0.0.1p0             
HELLO-MOTOR-ARM           | Downgrading to Stepper.v0.0.4p0          
------------------------------------------------
WARNING: (1) Updating robot firmware should only be done by experienced users
WARNING: (2) Do not have other robot processes running during update
WARNING: (3) Leave robot powered on during update
WARNING: (4) Ensure Lift has support clamp in place
WARNING: (5) Lift may make a loud noise during programming. This is normal.
Proceed with update?? [y/N]:
```
Review the recommendations and warnings before proceeding ('y'). If you prefer to only update one or more boards you can specify it on the command line. For example:
```bash
RE1_firmware_updater.py --install --arm --wacc
```
## Other Useful Commands

Running  `RE1_firmware_updater.py --current` will report the currently install firmware: 
```bash
>>$RE1_firmware_updater.py --current
######################################## Currently Installed Firmware ########################################
------------ HELLO-WACC ------------
Installed Firmware: Wacc.v0.0.2p1
Installed Stretch Body supports protocols: p0 , p1
Installed protocol p1 : VALID
------------ HELLO-MOTOR-LIFT ------------
Installed Firmware: Stepper.v0.1.0p1
Installed Stretch Body supports protocols: p0 , p1
Installed protocol p1 : VALID
------------ HELLO-PIMU ------------
Installed Firmware: Pimu.v0.0.2p1
Installed Stretch Body supports protocols: p0 , p1
Installed protocol p1 : VALID
------------ HELLO-MOTOR-ARM ------------
Installed Firmware: Stepper.v0.1.0p1
Installed Stretch Body supports protocols: p0 , p1
Installed protocol p1 : VALID
------------ HELLO-MOTOR-LEFT-WHEEL ------------
Installed Firmware: Stepper.v0.1.0p1
Installed Stretch Body supports protocols: p0 , p1
Installed protocol p1 : VALID
------------ HELLO-MOTOR-RIGHT-WHEEL ------------
Installed Firmware: Stepper.v0.1.0p1
Installed Stretch Body supports protocols: p0 , p1
Installed protocol p1 : VALID

```

Running  `RE1_firmware_updater.py --available` will list the available versions on GitHub:

```bash
>>$ RE1_firmware_updater.py --available
Collecting information...
####################### Currently Tagged Versions of Stretch Firmware on Master Branch #######################
---- HELLO-WACC ----
Wacc.v0.0.1p0
---- HELLO-MOTOR-LIFT ----
Stepper.v0.0.1p0
Stepper.v0.0.2p0
Stepper.v0.0.3p0
Stepper.v0.0.4p0
---- HELLO-PIMU ----
Pimu.v0.0.1p0
---- HELLO-MOTOR-ARM ----
Stepper.v0.0.1p0
Stepper.v0.0.2p0
Stepper.v0.0.3p0
Stepper.v0.0.4p0
---- HELLO-MOTOR-LEFT-WHEEL ----
Stepper.v0.0.1p0
Stepper.v0.0.2p0
Stepper.v0.0.3p0
Stepper.v0.0.4p0
---- HELLO-MOTOR-RIGHT-WHEEL ----
Stepper.v0.0.1p0
Stepper.v0.0.2p0
Stepper.v0.0.3p0
Stepper.v0.0.4p0
```

## Appendix: Install Arduino CLI
In some cases it may be necessary to manually install the Arduino command line tool

Check if the [Arduino Cli](https://github.com/arduino/arduino-cli) tool is already installed with version 1.6.21 of the SAMD package:

```bash
>>$ arduino-cli core list
ID               Installed Latest Name                                        
arduino:samd     1.6.21    1.6.21 Arduino SAMD Boards (32-bits ARM Cortex-M0+)
```

If not:

```bash
>>$ cd ~/repos
>>$ git clone https://github.com/hello-robot/stretch_install
>>$ cd stretch_install/factory
>>$ ./stretch_install_arduino.sh
```

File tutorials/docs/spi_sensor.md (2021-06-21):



# Integrating an SPI Device

This tutorial illustrates the integration of a SPI device on to the [Wrist Expansion header](https://docs.hello-robot.com/hardware_user_guide/#wrist). It extends the [Data Transfer](./data_transfer.md) tutorial. We recommend doing this tutorial prior to doing this one.

# Calculator via SPI

In this tutorial we will run the calculator from the [Data Transfer](./data_transfer.md) tutorial on an Adafruit Metro M0 Express (Arduino Zero) that is running as an SPI slave. It will take a calculator `Command` from the Wacc and return the result in `Status` message. 



### Flash Firmware

First, program the Metro with the provided sketch, [zero_wacc_spi](../arduino/zero_wacc_spi). Be sure to:

* Select the board's port from the IDE under Tools/Port
* Select the board 'Adafruit M0 Express' from the IDE under Tools/Board

Next, program the Wacc with the provided sketch, [hello_wacc_spi](../arduino/hello_wacc_spi). Be sure to:

* Select the board's port from the IDE under Tools/Port
* Select the board 'Hello Wacc' from the IDE under Tools/Board

### Code Walk-through

The code is straightforward and is a natural extension of the code described in the  [Data Transfer](./data_transfer.md) tutorial. A few sections to highlight in the  [hello_wacc_spi](../arduino/hello_wacc_spi) sketch are:

First, in the sketch `setup()` we configure the slave select pin to be an output

```c
pinMode(HEADER_SPI_SS,OUTPUT);
```

Next in `setupWacc()` we add code to configure the SPI

```c
SPISettings settingsA(100000, MSBFIRST, SPI_MODE1);
SPI.begin();
SPI.beginTransaction(settingsA);
```

In `Wacc.cpp` we add the SPI code:

```c
#include <SPI.h>

uint8_t spi_out[9];   //SPI data out
uint8_t spi_in[9];    //SPI data in
uint8_t ds_spi_cnt=0; //Down sample counter
float FS_SPI = 10;    //Rate to run transactions (Hz)

void spiTransaction()
{
  digitalWrite(HEADER_SPI_SS, LOW);
  SPI.transfer('X'); //Mark start of transaction
  memcpy(spi_out, (uint8_t *) (&cmd.calc), sizeof(Calc_Command));
  for (uint8_t idx = 0; idx < 9; idx++)
    spi_in[idx] = SPI.transfer(spi_out[idx]);
  digitalWrite(HEADER_SPI_SS, HIGH);
  memcpy((uint8_t *) (&stat.calc),spi_in+1,  sizeof(Calc_Status));
}
```

Here, the 9 bytes of the `Calc_Command` are transferred out and the 4 bytes of the `Calc_Status` are received. 

**Note: This simple communication protocol is not robust, using an 'X' to demarcate the start of a transaction**

Finally, we call the `spiTransaction()` function at a rate of `FS_SPI` by adding to `stepWaccController()`:

```c
 if (ds_spi_cnt++ >= (FS_CTRL / FS_SPI))
  {
    ds_spi_cnt = 0;
    spiTransaction();
  }
```

### Wire Up the Boards

Next, wire the Metro to the Expansion Header as:

| Stretch Expansion Header | Uno  |
| --- | ---- |
| SS | SS |
| MISO | MISO |
| MOSI | MOSI |
| SCK | SCK  |
| GND | GND  |

**Note: Other Arduino boards can be used. However 5V Arduinos boards will need their SPI lines level shifted to 3V3.**

### Test the Calculator

Now, test the setup using the provided tool, [stretch_wacc_calc_jog.py](../python/stretch_wacc_calc_jog.py). As shown below, The Arduino Uno performs the calculation of 12*13 and the result is report back to Stretch Body.

```bash
hello-robot@stretch-re1-100x:~$ cd repos/stretch_firmware/tutorial/python/
hello-robot@stretch-re1-100x:~/repos/stretch_firmware/tutorial/python$ ./stretch_wacc_calc_jog.py 
------ MENU -------
m: menu
r: reset board
a: set D2 on
b: set D2 off
c: set D3 on
d: set D3 off
X: do calculation
-------------------
X
---Calculate Op(Var1,Var2) ---
Op=0: Add
Op=1: Mult
Op=2: Div
Enter Op
1
Enter Var1
12
Enter Var2
13
------ MENU -------
m: menu
r: reset board
a: set D2 on
b: set D2 off
c: set D3 on
d: set D3 off
X: do calculation
-------------------

------------------------------
Ax (m/s^2) 0.0488623343408
Ay (m/s^2) 0.155020624399
Az (m/s^2) -10.0049753189
A0 349
D0 (In) 0
D1 (In) 1
D2 (Out) 70
D3 (Out) 0
Single Tap Count 26
State  0
Debug 0
Timestamp 1591588745.27
Board version: Wacc.Guthrie.V1
Firmware version: Wacc.v0.0.1pMySPI
Calc: 156.0
------ MENU -------
m: menu
r: reset board
a: set D2 on
b: set D2 off
c: set D3 on
d: set D3 off
X: do calculation
-------------------

```

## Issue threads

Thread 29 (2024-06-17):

Add a filter that turns on the fan when internal temperature is too high

hello-binit, 2024-06-17:

hello-binit, 2024-06-17:
From Yi-Che: "I've also noticed that toggling run-stop will turn off both fans, not sure if this behavior is intended". This is when using the `Pimu.set_fan_on()` API in Stretch Body.

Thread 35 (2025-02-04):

Drift at zero accel

aedsinger, 2025-02-04:
When stepper is in incremental trajectory mode
* Command zero incremental motion with zero acceleration
* Motor will drive very slowly
* Issue in in the motiongenerator.cpp where values are divided by zero

hello-binit, 2025-02-04:
@aedsinger should commands with zero acceleration be rejected?

aedsinger, 2025-02-04:
Not sure, it seems that bad accel values aren't the only issue. Will need
to dig in.

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

--
Aaron Edsinger, PhD <http://www.linkedin.com/in/aaron-edsinger>
co-founder & CEO
Hello Robot Inc

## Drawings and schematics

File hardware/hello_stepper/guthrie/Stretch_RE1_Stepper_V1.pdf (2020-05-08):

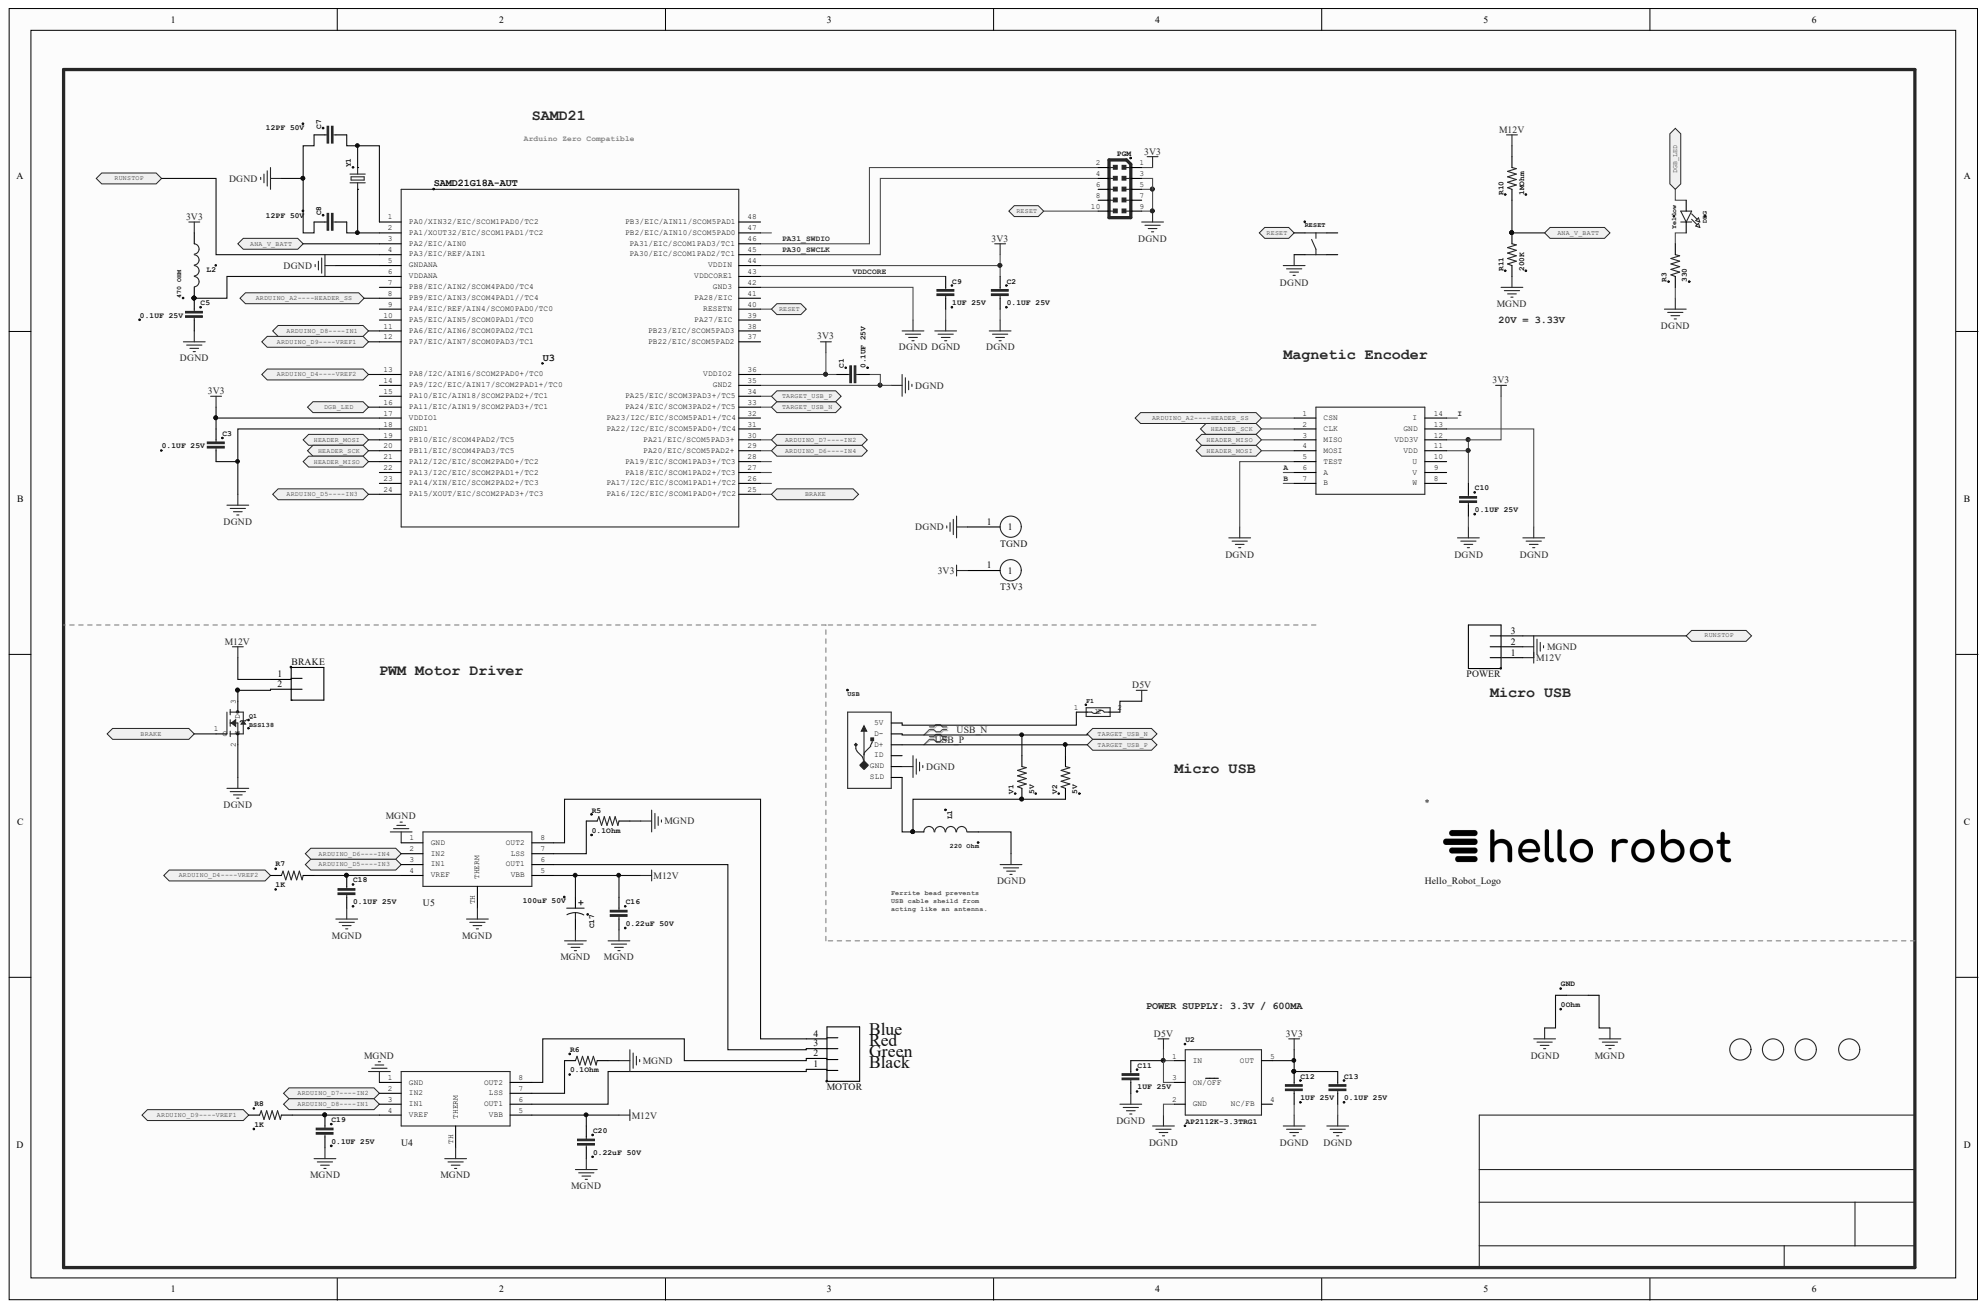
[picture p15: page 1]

0.1UF 25V Blue Red Green Black

Ferrite bead prevents
USB cable sheild from
acting like an antenna.

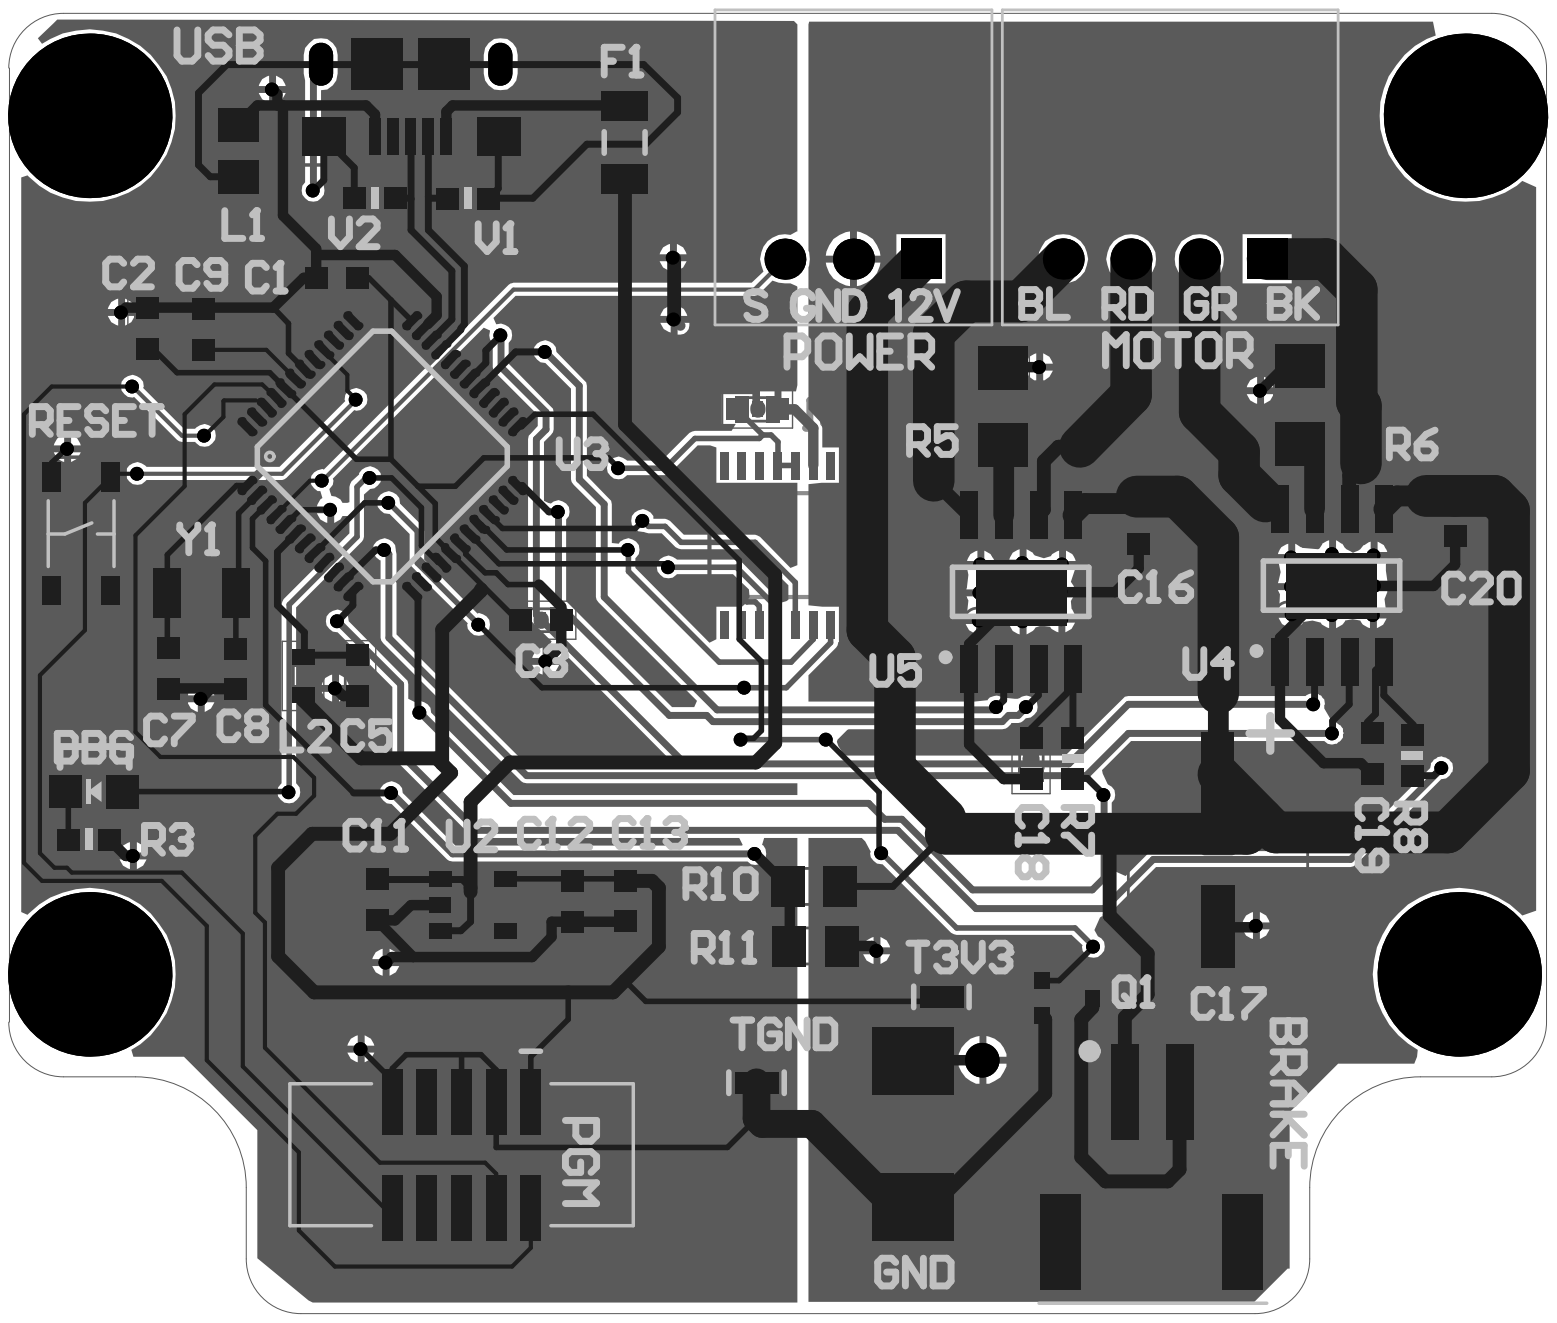
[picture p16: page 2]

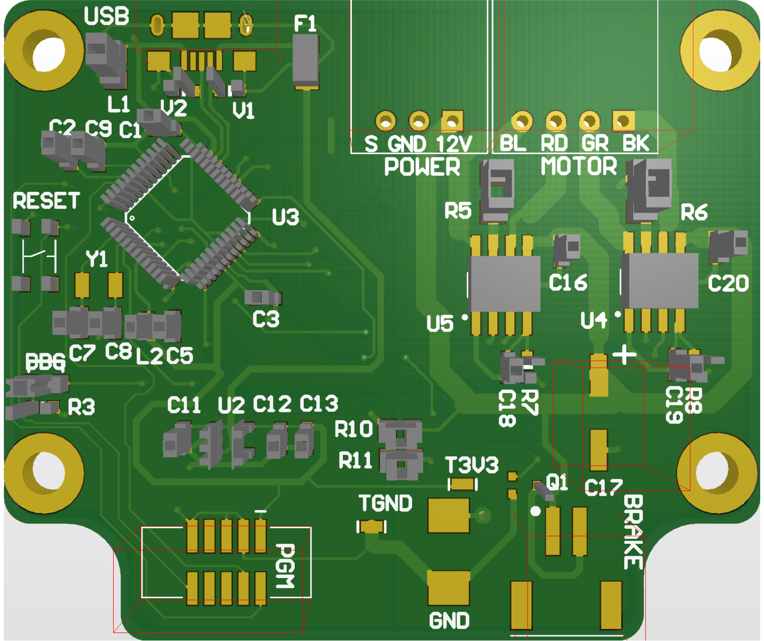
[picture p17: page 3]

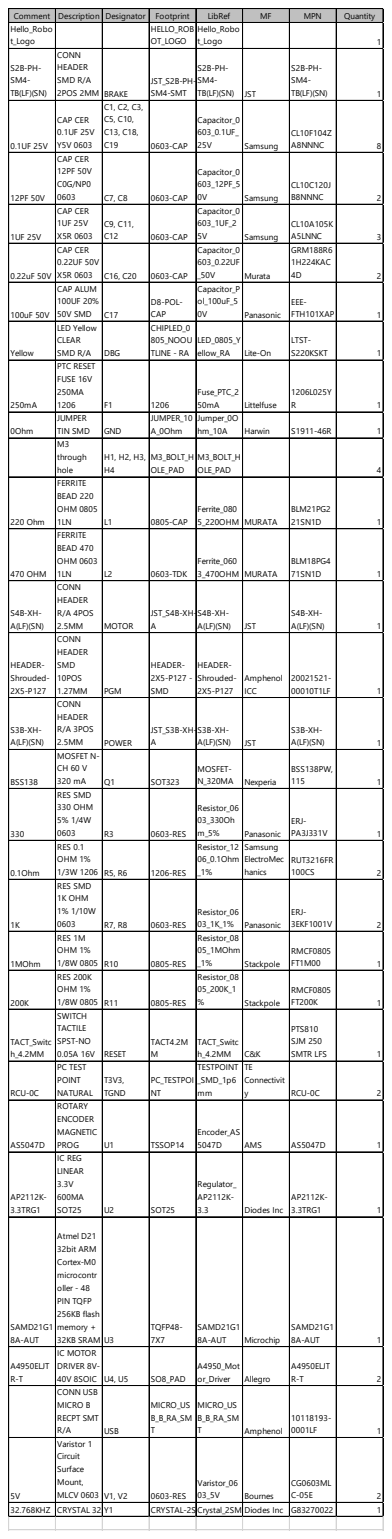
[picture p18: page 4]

Comment | Description | Designator | Footprint | LibRef | MF | MPN | Quantity
Hello_Robo t_Logo | | | HELLO_ROB OT_LOGO | Hello_Robo t_Logo | | | 1

S2B-PH-SM4-TB(LF)(SN) | CONN HEADER SMD R/A 2POS 2MM | BRAKE | JST_S2B-PH-SM4-SMT | S2B-PH-SM4-TB(LF)(SN) | JST | S2B-PH-SM4-TB(LF)(SN) | 1

0.1UF 25V | CAP CER 0.1UF 25V Y5V 0603 | C1, C2, C3, C5, C10, C13, C18, C19 | 0603-CAP | Capacitor_0 603_0.1UF_ 25V | Samsung | CL10F104Z A8NNNC | 8

12PF 50V | CAP CER 12PF 50V C0G/NP0 0603 | C7, C8 | 0603-CAP | Capacitor_0 603_12PF_5 0V | Samsung | CL10C120J B8NNNC | 2

1UF 25V | CAP CER 1UF 25V X5R 0603 | C9, C11, C12 | 0603-CAP | Capacitor_0 603_1UF_2 5V | Samsung | CL10A105K A5LNNC | 3

0.22uF 50V | CAP CER 0.22UF 50V X5R 0603 | C16, C20 | 0603-CAP | Capacitor_0 603_0.22UF _50V | Murata | GRM188R6 1H224KAC 4D | 2

100uF 50V | CAP ALUM 100UF 20% 50V SMD | C17 | D8-POL-CAP | Capacitor_P ol_100uF_5 0V | Panasonic | EEE-FTH101XAP | 1

Yellow | LED Yellow CLEAR SMD R/A | DBG | CHIPLED_0 805_NOOU TLINE - RA | LED_0805_Y ellow_RA | Lite-On | LTST-S220KSKT | 1

250mA | PTC RESET FUSE 16V 250MA 1206 | F1 | 1206 | Fuse_PTC_2 50mA | Littelfuse | 1206L025Y R | 1

0Ohm | JUMPER TIN SMD | GND | JUMPER_10 A_0Ohm | Jumper_0O hm_10A | Harwin | S1911-46R | 1

M3 through hole | H1, H2, H3, H4 | M3_BOLT_H OLE_PAD | M3_BOLT_H OLE_PAD | | | 4

220 Ohm | FERRITE BEAD 220 OHM 0805 1LN | L1 | 0805-CAP | Ferrite_080 5_220OHM | MURATA | BLM21PG2 21SN1D | 1

470 OHM | FERRITE BEAD 470 OHM 0603 1LN | L2 | 0603-TDK | Ferrite_060 3_470OHM | MURATA | BLM18PG4 71SN1D | 1

S4B-XH-A(LF)(SN) | CONN HEADER R/A 4POS 2.5MM | MOTOR | JST_S4B-XH-A | S4B-XH-A(LF)(SN) | JST | S4B-XH-A(LF)(SN) | 1

HEADER-Shrouded-2X5-P127 | CONN HEADER SMD 10POS 1.27MM | PGM | HEADER-2X5-P127 -SMD | HEADER-Shrouded-2X5-P127 | Amphenol ICC | 20021521-00010T1LF | 1

S3B-XH-A(LF)(SN) | CONN HEADER R/A 3POS 2.5MM | POWER | JST_S3B-XH-A | S3B-XH-A(LF)(SN) | JST | S3B-XH-A(LF)(SN) | 1

BSS138 | MOSFET N-CH 60 V 320 mA | Q1 | SOT323 | MOSFET-N_320MA | Nexperia | BSS138PW, 115 | 1

330 | RES SMD 330 OHM 5% 1/4W 0603 | R3 | 0603-RES | Resistor_06 03_330Oh m_5% | Panasonic | ERJ-PA3J331V | 1

0.1Ohm | RES 0.1 OHM 1% 1/3W 1206 | R5, R6 | 1206-RES | Resistor_12 06_0.1Ohm _1% | Samsung ElectroMec hanics | RUT3216FR 100CS | 2

1K | RES SMD 1K OHM 1% 1/10W 0603 | R7, R8 | 0603-RES | Resistor_06 03_1K_1% | Panasonic | ERJ-3EKF1001V | 2

1MOhm | RES 1M OHM 1% 1/8W 0805 | R10 | 0805-RES | Resistor_08 05_1MOhm _1% | Stackpole | RMCF0805 FT1M00 | 1

200K | RES 200K OHM 1% 1/8W 0805 | R11 | 0805-RES | Resistor_08 05_200K_1 % | Stackpole | RMCF0805 FT200K | 1

TACT_Switc h_4.2MM | SWITCH TACTILE SPST-NO 0.05A 16V | RESET | TACT4.2M M | TACT_Switc h_4.2MM | C&K | PTS810 SJM 250 SMTR LFS | 1

RCU-0C | PC TEST POINT NATURAL | T3V3, TGND | PC_TESTPOI NT | TESTPOINT _SMD_1p6 mm | TE Connectivit y | RCU-0C | 2

AS5047D | ROTARY ENCODER MAGNETIC PROG | U1 | TSSOP14 | Encoder_AS 5047D | AMS | AS5047D | 1

AP2112K-3.3TRG1 | IC REG LINEAR 3.3V 600MA SOT25 | U2 | SOT25 | Regulator_ AP2112K-3.3 | Diodes Inc | AP2112K-3.3TRG1 | 1

SAMD21G1 8A-AUT | Atmel D21 32bit ARM Cortex-M0 microcontr oller - 48 PIN TQFP 256KB flash memory + 32KB SRAM | U3 | TQFP48-7X7 | SAMD21G1 8A-AUT | Microchip | SAMD21G1 8A-AUT | 1

A4950ELJT R-T | IC MOTOR DRIVER 8V-40V 8SOIC | U4, U5 | SO8_PAD | A4950_Mot or_Driver | Allegro | A4950ELJT R-T | 2

CONN USB MICRO B RECPT SMT R/A | USB | MICRO_US B_B_RA_SM T | MICRO_US B_B_RA_SM T | Amphenol | 10118193-0001LF | 1

5V | Varistor 1 Circuit Surface Mount, MLCV 0603 | V1, V2 | 0603-RES | Varistor_06 03_5V | Bournes | CG0603ML C-05E | 2

32.768KHZ | CRYSTAL 32.7Y1 | | CR YSTAL-2SCrystal_2SMDDiodes Inc | | | G83270022 | 1

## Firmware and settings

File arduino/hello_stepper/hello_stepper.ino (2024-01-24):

/*
  -------------------------------------------------------------
  Hello Robot - Hello Stepper

  This code is derived from the Mechaduino project. 
  https://github.com/jcchurch13/Mechaduino-Firmware

  All materials released under the GNU General Public License v3.0 (GNU GPLv3).
  https://www.gnu.org/licenses/gpl-3.0.html  

  Copyright (c) 2020 by Hello Robot Inc.
  --------------------------------------------------------------
*/


#include "Utils.h"
#include "Parameters.h"
#include "State.h"
#include "analogFastWrite.h"

#ifdef HELLO
#include "HelloController.h"
#include "Transport.h"
#endif

//////////////////////////////////////
/////////////////SETUP////////////////
//////////////////////////////////////



void setup()        // This code runs once at startup
{                         

  
  digitalWrite(ledPin,HIGH);        // turn LED on 
  setupPins();                      // configure pins
  setupTCInterrupts();              // configure controller interrupt
  

  SerialUSB.begin(2000000); 
  
#ifndef HELLO  
  //delay(3000);                      // This delay seems to make it easier to establish a connection when the Mechaduino is configured to start in closed loop mode.  
  serialMenu();     // Prints menu to serial monitor
#else
  setupBoardVariants();  
  setupMGInterrupts();
#endif
 
  setupSPI();                       // Sets up SPI for communicating with encoder
  digitalWrite(ledPin,LOW);         // turn LED off 
  
  // spot check some of the lookup table to decide if it has been filled in
  //if (lookup[0] == 0 && lookup[128] == 0 && lookup[1024] == 0)
  //  SerialUSB.println("WARNING: Lookup table is empty! Run calibration");

  // Uncomment the below lines as needed for your application.
  // Leave commented for initial calibration and tuning.
  
  //    configureStepDir();           // Configures setpoint to be controlled by step/dir interface
  //    configureEnablePin();         // Active low, for use wath RAMPS 1.4 or similar
  //     enableTCInterrupts();         // uncomment this line to start in closed loop 
  //    mode = 'x';                   // start in position mode
#ifdef HELLO
    setupTransport();
    setupHelloController();
    enableTCInterrupts();  //Always be running the loop
    enableMGInterrupts();
    enableMotorDrivers(); //Turn on now that gains are loaded
#endif
setupWDT(WDT_TIMEOUT_PERIOD);
enableMotorDecay(); //Needed for Brake circuit on lift stepper board 
}
  


//////////////////////////////////////
/////////////////LOOP/////////////////
//////////////////////////////////////


void loop()                 // main loop
{

#ifdef HELLO
//Flash LED fast when in menu mode, slow in RPC mode
if (hello_interface)
{
  resetWDT();
  stepHelloControllerRPC();
}
else
{
  disableWDT();
  serialCheck();
  toggle_led(200);
}
#else
  disableWDT();
  serialCheck();              //must have this execute in loop for serial commands to function
#endif


}

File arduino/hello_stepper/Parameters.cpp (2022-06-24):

/*
  -------------------------------------------------------------
  Hello Robot - Hello Stepper

  This code is derived from the Mechaduino project. 
  https://github.com/jcchurch13/Mechaduino-Firmware

  All materials released under the GNU General Public License v3.0 (GNU GPLv3).  
  https://www.gnu.org/licenses/gpl-3.0.html

  Copyright (c) 2020 by Hello Robot Inc.
  --------------------------------------------------------------
*/


//Contains the Mechaduino parameter defintions


#include <Wire.h>
#include "Parameters.h"
#include "math.h"


//----Current Parameters-----

/////////////////////////////////////////////////
#ifdef HELLO 
#include "Common.h"

//In contrast to stock Mechaduino code, all actuator specific parameters are zero by default. 
//The paramater data is stored in YAML and required to be pushed down at startup

//Default parameters used in Menu Mode
volatile float Fs = 6500.0;   //Sample frequency in Hz

volatile float pKp = 0.0;      //position mode PID values.  Depending on your motor/load/desired performance, you will need to tune these values.  You can also implement your own control scheme
volatile float pKi = 0.0;
volatile float pKd = 0.0;
volatile float pLPF = 0;       //break frequency in hertz


volatile float vKp = 0.0;       //velocity mode PID values.  Depending on your motor/load/desired performance, you will need to tune these values.  You can also implement your own control scheme
volatile float vKi = 0.0;
volatile float vKd = 0.0;
volatile float vLPF = 0.0;       //break frequency in hertz


const int spr = 200;                // 200 steps per revolution  -- for 400 step/rev, you should only need to edit this value
const float aps = 360.0/ spr;       // angle per step
int cpr = 16384;                    // counts per rev
const float stepangle = aps/32.0;   // for step/dir interrupt: aps/32 is the equivalent of 1/32 microsteps

volatile float pLPFa = exp(pLPF*-2*3.14159/Fs); // z = e^st pole mapping
volatile float pLPFb = (1.0-pLPFa);
volatile float vLPFa = exp(vLPF*-2*3.14159/Fs); // z = e^st pole mapping
volatile float vLPFb = (1.0-vLPFa)* Fs * 0.16666667;

//Encoder calibration.
const float __attribute__((__aligned__(256))) lookup[16384] = {};

//NOTE: This is recomputed in setupBoardVariants based on the variant ID as can depend on the board version
//The board uses two  A4950ELJTR motor drivers. These are capable of 3.5A peak currents.
// An iMax of 3.2A results in a uMax of 247. By default set at 8-bit pwm. 
volatile float iMAX =3.2;        // Be careful adjusting this.  
volatile float rSense = 0.1;   //Ohms per Franco board
volatile int uMAX = (255/3.3)*(iMAX*10*rSense);   


//PA default is 1.8 degrees. 
//Adjusting PA (phase advance) sets the max velocity achieved during commutation
//PA of 2.8 = runaway
//PA of 2.5 = fast
//PA of 1.8 = nominal
volatile float PA = 1.8; //aps;            // Phase advance...aps = 1.8 (default) for 200 steps per rev, 0.9 for 400

/////////////////////////////////////////////////
#else

volatile float Fs = 6500.0;   //Sample frequency in Hz

volatile float pKp = 15.0;      //position mode PID values.  Depending on your motor/load/desired performance, you will need to tune these values.  You can also implement your own control scheme
volatile float pKi = 0.2;
volatile float pKd = 250.0;//1000.0;
volatile float pLPF = 30;       //break frequency in hertz

volatile float vKp = 0.001;       //velocity mode PID values.  Depending on your motor/load/desired performance, you will need to tune these values.  You can also implement your own control scheme
volatile float vKi = 0.001;
volatile float vKd = 0.0;
volatile float vLPF = 100.0;       //break frequency in hertz

// This is the encoder lookup table (created by calibration routine):


const float __attribute__((__aligned__(256))) lookup[16384] = {};


volatile float pLPFa = exp(pLPF*-2*3.14159/Fs); // z = e^st pole mapping
volatile float pLPFb = (1.0-pLPFa);
volatile float vLPFa = exp(vLPF*-2*3.14159/Fs); // z = e^st pole mapping
volatile float vLPFb = (1.0-vLPFa)* Fs * 0.16666667;

const int spr = 200;                // 200 steps per revolution  -- for 400 step/rev, you should only need to edit this value
const float aps = 360.0/ spr;       // angle per step
int cpr = 16384;                    // counts per rev
const float stepangle = aps/32.0;   // for step/dir interrupt: aps/32 is the equivalent of 1/32 microsteps

volatile float PA = aps;            // Phase advance...aps = 1.8 for 200 steps per rev, 0.9 for 400

const float iMAX = 1.8;             // Be careful adjusting this.  While the A4954 driver is rated for 2.0 Amp peak currents, it cannot handle these currents continuously.  Depending on how you operate the Mechaduino, you may be able to safely raise this value...please refer to the A4954 datasheet for more info
const float rSense = 0.1;
volatile int uMAX = (255/3.3)*(iMAX*10*rSense);   // 255 for 8-bit pwm, 1023 for 10 bit, must also edit analogFastWrite

#endif
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

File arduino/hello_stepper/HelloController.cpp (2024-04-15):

/*
/*
  -------------------------------------------------------------
  Hello Robot - Hello Stepper

  This code is derived from the Mechaduino project. 
  https://github.com/jcchurch13/Mechaduino-Firmware
  
  All materials released under the GNU General Public License v3.0 (GNU GPLv3).
  https://www.gnu.org/licenses/gpl-3.0.html

  Copyright (c) 2020 by Hello Robot Inc.
  --------------------------------------------------------------
*/

#include "HelloController.h"
#include "State.h"
#include "Utils.h"
#include "Parameters.h"
#include "VelocityGenerator.h"
#include "MotionGenerator.h"
#include "analogFastWrite.h"
#include "Transport.h"
#include <SPI.h>
#include "analogFastWrite.h"
#include <FlashStorage.h>
#include "Controller.h"

#include "SyncManager.h"
#include "TimeManager.h"
#include "TrajectoryManager.h"
#include "TraceManager.h"

#include "AnalogManager.h"

void write_to_lookup(uint8_t page_id, float * data);


Command cmd,cmd_in;
CommandReply cmd_reply;
Gains gains, gains_in;
Trigger trg, trg_in;
Status stat,stat_out;
StatusAux stat_aux;
EncCalib enc_calib_in;
MotionLimits motion_limits;
TrajectorySegment traj_seg_in;
TrajectorySegmentReply traj_seg_reply;

Stepper_Board_Info board_info;
FlashStorage(flash_gains, Gains);
FlashStorage(flash_stepper_type, uint8_t);



LoadTest load_test;
volatile int dirty_cmd=false;
volatile int sync_irq_cnt_last=0;
volatile bool dirty_gains=false;
volatile bool dirty_trigger=false;
volatile bool dirty_traj_seg=false;
volatile bool dirty_trigger_mark_on_contact=false;

volatile bool diag_pos_calibrated = 0;
volatile bool diag_runstop_on=0;
volatile bool diag_near_pos_setpoint=0;
volatile bool diag_near_vel_setpoint=0;
volatile bool diag_is_moving=0;
volatile bool diag_at_current_limit=0;
volatile bool diag_is_mg_accelerating=0;
volatile bool diag_is_mg_moving=0;
volatile bool diag_calibration_rcvd=0;
volatile bool diag_waiting_on_sync=0;


int switch_to_menu_cnt=0;
int board_reset_cnt=0;
int guarded_event_cnt=0;
int guarded_eff_cnt=0;
#define GUARDED_EFF_THRESH 50 // (ms) Must be over effort for this long to trigger a contact event
bool motion_limits_set=0;
volatile int cmd_cnt_exec=0;
volatile int cmd_cnt_rpc=0;
volatile int cmd_rpc_overflow=0;

#define N_POS_HISTORY 250 //With TC4_LOOP_RATE 1000, log 0.25s of past motions
float pos_history[N_POS_HISTORY];
int pos_history_idx=0;


//By default boot with hello_interface on
//Turn on when get RPC request RPC_SET_MENU_ON
//Turn back off when menu gets 'z' command
volatile bool hello_interface = 1;
float mark_pos=0.0;
float mark_rem=0.0;
float mark_on_contact_pos=0.0;
float ywc=0;
float uMAX_P=0;
float uMAX_N=0;
float uMAX_PF=0;
float uMAX_NF=0;
int cntr=0;
volatile uint16_t ctrl_cycle_cnt=0;

//Filter params    
volatile float efLPFa = 0.0; 
volatile float efLPFb = 1.0;
volatile float efLPF = 0;
volatile float vsLPF = 0.0;  
volatile float vsLPFa = 0.0; 
volatile float vsLPFb = 1.0;

  
bool first_filter=true;

bool led_on=false;
unsigned long t_toggle_last=0;
float hold_pos=0;
float traj_hold_pos=0;

void update_status();

VelocityGenerator vg;
MotionGenerator mg;



float vs=0;
float eff=0;
float g_eff_pos=0;
float g_eff_neg=0;
double ywd=0;
float PAY = 0;

float FsCtrl = TC4_LOOP_RATE;
bool receiving_calibration=false;
bool flip_encoder_polarity = false;
bool flip_effort_polarity = false;


bool runstop_enabled=false;
bool guarded_mode_enabled = false;

bool safety_override = false;
bool guarded_override=false;
int first_step_safety=10; //count down
uint8_t board_id=0;

int vel_watchdog=TC4_LOOP_RATE; //Watchdog counts down from 1s
bool motor_enabled_flag = true;


///////////////////////// UTIL ///////////////////////////


float deg_to_rad(float x)
{
  return x*0.017453292519943295;
}
float rad_to_deg(float x)
{
  return x*57.29577951308232;
}

float k_c2e; 
float k_e2c; 

float current_to_effort(float x)
{
  return max(-255,min(255,x*k_c2e));
}

#define NOMINAL_BUS_VOLTAGE 12.5 //V of battery fully charged, no charger attached, nominal load
#define RAW_TO_VOLTAGE 20.0/1024 //10bit adc, 0-20V per 0-3.3V reading
float voltage_calibrated=0;
float get_voltage_calibrated(float raw)
{
 return (raw*RAW_TO_VOLTAGE)-0.3; //0.3 is needed to account for leakage current of TVS
}

//This returns an effort value (-255 to 255) that is normalized by the bus voltage
//such that as the bus voltage drops, the estimate of effort "force" applied to the outside world
//goes down for a given current
//Only works for VARIANT_3 and later boards

float current_to_effort_v_norm(float x)
{
    float e=current_to_effort(x);
   if (BOARD_VARIANT>=3 && voltage_calibrated!=0)
   {
    return max(-255,min(255,e*voltage_calibrated/NOMINAL_BUS_VOLTAGE));
   }
   else
    return e;
}

float effort_to_current(float e)
{
  return (e*k_e2c);

}

void toggle_led(int rate_ms)
{
  unsigned long t = time_manager.get_elapsed_time_ms();
  if (t-t_toggle_last>rate_ms)
  {
    t_toggle_last=t;
    if (!led_on)
          digitalWrite(ledPin, HIGH);  //LED
      else
          digitalWrite(ledPin,LOW);   //LED
     led_on=!led_on;
  }
}



uint8_t    BOARD_VARIANT;
uint8_t    BOARD_VARIANT_DRV8842;
uint8_t    BOARD_VARIANT_PIN_RUNSTOP;
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

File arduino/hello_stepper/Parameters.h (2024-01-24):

/*
  -------------------------------------------------------------
  Hello Robot - Hello Stepper

  This code is derived from the Mechaduino project. 
  https://github.com/jcchurch13/Mechaduino-Firmware
  
  All materials released under the GNU General Public License v3.0 (GNU GPLv3).  
  https://www.gnu.org/licenses/gpl-3.0.html

  Copyright (c) 2020 by Hello Robot Inc.
  --------------------------------------------------------------
*/

//Contains the Mechaduino parameter declarations

#ifndef __PARAMETERS_H__
#define __PARAMETERS_H__



#define HELLO   //Turn on and off the Hello Codebase

#ifdef HELLO
#define firmware_version "0.1"            //firmware version
#define identifier "Hello Stepper"       // change this to help keep track of multiple mechaduinos (printed on startup)
#else
#define firmware_version "0.1.5"    //firmware version
#define identifier "x"              // change this to help keep track of multiple mechaduinos (printed on startup)
#endif

//----Current Parameters-----

extern volatile float Ts;
extern volatile float Fs;

extern volatile float pKp;
extern volatile float pKi;
extern volatile float pKd;
extern volatile float pLPF;


extern volatile float vKp;
extern volatile float vKi;
extern volatile float vKd;
extern volatile float vLPF;

extern const float lookup[];


extern volatile float pLPFa;
extern volatile float pLPFb;
extern volatile float vLPFa;
extern volatile float vLPFb;


extern const int spr; //  200 steps per revolution
extern const float aps; // angle per step
extern int cpr; //counts per rev
extern const float stepangle;

extern volatile float PA;  //

extern volatile float iMAX;
extern volatile float rSense;
extern volatile int uMAX;


extern const int sin_1[];

//Defines for pins:

#define IN_4  6
#define IN_3  5
#define VREF_2 4
#define VREF_1 9
#define IN_2  7
#define IN_1  8

#ifdef HELLO
#define ledPin  0
//Pins for DRV8842
#define DRV8842_FAULT_A 17 //PA4
#define DRV8842_FAULT_B 18 //PA5
#define DRV8842_NSLEEP_A 38 //PA13
#define DRV8842_NSLEEP_B 2 //PA14
#define MOTOR_SHUNT 35 //PA16
#define DRV8842_DECAY 10 //PA18

#else
#define ledPin  13
#endif

#define chipSelectPin A2 //output to chip select

#define step_pin 1
#define dir_pin 0
#define enable_pin 2

//for faster digitalWrite:
#define IN_1_HIGH() (REG_PORT_OUTSET0 = PORT_PA06)
#define IN_1_LOW() (REG_PORT_OUTCLR0 = PORT_PA06)
#define IN_2_HIGH() (REG_PORT_OUTSET0 = PORT_PA21)
#define IN_2_LOW() (REG_PORT_OUTCLR0 = PORT_PA21)
#define IN_3_HIGH() (REG_PORT_OUTSET0 = PORT_PA15)
#define IN_3_LOW() (REG_PORT_OUTCLR0 = PORT_PA15)
#define IN_4_HIGH() (REG_PORT_OUTSET0 = PORT_PA20)
#define IN_4_LOW() (REG_PORT_OUTCLR0 = PORT_PA20)

#ifdef HELLO
#define ledPin_HIGH() (REG_PORT_OUTSET0 = PORT_PA11)
#define ledPin_LOW() (REG_PORT_OUTCLR0 = PORT_PA11)
#else
#define ledPin_HIGH() (REG_PORT_OUTSET0 = PORT_PA17)
#define ledPin_LOW() (REG_PORT_OUTCLR0 = PORT_PA17)
#endif

#define CHIPSELECT_HIGH() (REG_PORT_OUTSET1 = PORT_PB09)
#define CHIPSELECT_LOW() (REG_PORT_OUTCLR1 = PORT_PB09)

#define ENABLE_PROFILE_IO    // Define to enable profiling I/O pins

#ifdef ENABLE_PROFILE_IO  
  #define TEST1   3

  #define TEST1_HIGH() (REG_PORT_OUTSET0 = PORT_PA09)
  #define TEST1_LOW() (REG_PORT_OUTCLR0 = PORT_PA09)

#else
  #define TEST1_HIGH()
  #define TEST1_LOW() 
#endif



#endif

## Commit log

2020-05-08 Initial public release v0.0.1
    [arduino_zero.cfg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]
2020-05-11 documentation of Arduino IDE improved
2020-06-08 arduino tutorials ready
2020-06-10 added level 5v note
2020-06-11 Added i2c tutorial
2020-11-20 stepper ts wip
2020-12-28 moved to command line Arduino install
2021-01-04 Fixed control mode switch bug per J-MIT
    [HelloController.cpp]
2021-01-04 Move to arduino command line and documentation
2021-01-05 Update stepper version to 0.0.2
2021-01-06 bump stepper firmware version to 0.2 for fix 009
    [Common.h]
2021-01-25 Remove stepper.h bug
2021-02-09 Bump board batch names
2021-04-07 rolled in vel_traj bug fix from master
    [HelloController.cpp]
2021-04-13 Bump stepper to 0.0.3 to capture stepper.h fix
    [Common.h]
2021-04-16 removed bug where lift jumps after calibration flash
    [HelloController.cpp]
2021-04-16 bump stepper to 0.0.4 given last fix
    [Common.h]
2021-05-01 Firmware support for reset of waypoint trajectory
    [Common.h, HelloController.cpp]
2021-05-05 Fixed the hold_traj bug so the value is always valid
    [HelloController.cpp]
2021-05-18 Tutorial on serial device ready
2021-05-18 added support for the DRV8842 stepper
2021-09-30 Introduce is_segment_valid and error messages
    [Common.h, HelloController.cpp]
2021-09-30 Mobile base steppers dont have soft motion limits
2021-09-30 Ensure the stepper is calibrated before checking joint limits
2021-09-30 is_segment_valid almost usable at reduced sample
2022-04-20 first pass on board id for stepper done
2022-04-20 stepper board id working
2022-04-21 first draft mitski stepper done
2022-04-26 neopixel working on pimu with dma
2022-05-02 ready for mitski pcba testing
2022-05-13 stepper spinning
2022-07-20 revised lightbar manager to be battery voltage based
2022-08-02 refactor lightbar ui. also fix trajectory bugs and cleanup
    [HelloController.cpp, hello_stepper.ino]
2022-08-05 Turn off stiffness slew on stepper. version bump
    [Common.h, HelloController.cpp]
2022-08-05 tag new stepper
2022-08-05 adjust stiffness slew rate
    [HelloController.cpp]
2022-08-12 wip homing
2022-08-15 wip motor shunt for lift
2022-09-14 fix pimu voltage display
    [Common.h, Pimu.cpp]
2023-03-03 Add velocity watchdog of 1s
2023-03-09 trace is working for all devices
2023-03-10 Reorg wacc timing to fix IRQ overruns
    [Common.h]
2023-03-13 added debug trace to stepper fw
2023-03-20 wip print trace
2023-03-21 wacc working with trace_manager
2023-03-22 done with trace refactor, all boards working
2023-06-13 Added WDT timer reset to hello_stepper
    [HelloController.cpp, HelloController.h, hello_stepper.ino]
2023-06-13 WDT timer added to hello_wacc
2023-06-13 Disable WDT on motor menu interface
2023-06-27 Halved the Trace raw data buffer
2023-07-05 Added WDT and trace memory fix to stepper
    [Common.h, HelloController.cpp, HelloController.h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]
2023-07-05 Added WDT and trace memory fix to Pimu
    [Common.h, Pimu.cpp]
2023-07-05 Added WDT and trace memory fix to Wacc
    [Common.h]
2023-07-28 Fixed trace rollover issue and move to int64 on motion gen
    [Common.h, HelloController.cpp, variant.h]
2023-09-07 Prince stepper ready
2023-09-14 imu working with irqs
2023-09-14 more imu
2023-10-06 cleanup imu
2023-10-06 fix voltage for s2 stepper
    [HelloController.cpp]
2023-10-10 fix pimu RE1 bugs
    [Common.h, Pimu.cpp]
2023-10-10 fix interrupt off bug
    [Pimu.cpp]
2023-10-11 Stepper remove analogread
2023-10-11 update stepper changelog
2023-11-06 Turn off SE3 IMU for now as causing RPC issues. Need to fix asap
    [Common.h, Pimu.cpp]
2023-11-20 imu orientation fix, and interrupt fix
    [Common.h, IMU_BNO085.cpp, Pimu.cpp]
2023-12-07 Added decay pin enabling for brake circuit
2023-12-09 adding charging class to pimu firmware
2023-12-12 fixed charging class code
    [Pimu.cpp]
2023-12-13 simpler charger detection, with only hotplug condition
2023-12-14 expermental charger detection
2023-12-14 adding board variant for s2
2023-12-16 finalized charger detection class
2023-12-16 fixed board variant
2023-12-18 switched counter increment to the top
2024-01-16 For stepper fw: Added stepper_type parameter in the board_info status. This allows us to now disable the motor drivers of the wheel stepper boards during a runstop event to allow for easy rotation of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
    [AnalogManager.cpp, Common.h, HelloController.cpp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]
2024-01-17 Added condition to not do analog_step for board variants less than Rev3
    Added condition to ensure no issue with the new analog manager class with older pcbs
    [HelloController.cpp]
2024-01-24 Changed major versions for both Pimu and stepper to 0.7.0p5
2024-02-16 guarded contact window and voltage norm working
2024-02-17 fix bug bad use of v global
    [Common.h, HelloController.cpp]
2024-02-17 version bump stepper
2024-02-26 generalize the motor driver off safety for base and arm
2024-04-15 bug fix to allow calibration of motors, due to the new feature of disabling the motor drivers while in saftey mode did not allow calibration to happen
    [Common.h, HelloController.cpp]

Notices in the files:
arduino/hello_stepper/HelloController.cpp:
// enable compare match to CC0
